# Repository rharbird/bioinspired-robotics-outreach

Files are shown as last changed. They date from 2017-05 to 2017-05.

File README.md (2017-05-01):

# UCL Bioinspired Robotics Summer School 2016

* Pictures here: https://flic.kr/s/aHskDVVoiB
* Note: In 2017 we will use the BBC Micro:bit JavaScript as the programming language for students with https://microbit.pxt.org.

## Snake Robot
* Designed by Dr Juan Gonzalez http://www.thingiverse.com/thing:13442
* C++ libraries for BBC Micro:bit, servo motors and Adafruit PCA9685 board, ( 16-Channel 12-bit PWM/Servo Driver, interface I2C board ) written by Professor Stephen Hailes, UCL.
* Teaching material written by Professor Stephen Hailes, UCL.

## Cockroach Robot
* Designed by Professor Stephen Hailes, UCL.
* C++ libraries for BBC Micro:bit, servo motors and Adafruit PCA9685 board, ( 16-Channel 12-bit PWM/Servo Driver, interface I2C board ) written by Professor Stephen Hailes, UCL.
* Teaching material written by Professor Stephen Hailes, UCL.

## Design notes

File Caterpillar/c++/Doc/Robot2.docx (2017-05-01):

# Microbit projects: caterpillar

## The aim

We’re going to build a crawling robot that’s inspired by some types of caterpillar. See:

https://www.youtube.com/watch?v=fRVGWCSij_M

or

https://www.youtube.com/watch?v=a9Km0edRFG4

In our case, we’ll only have 3 body segments but, as you can see from the video, a wave passes along the caterpillar so we’ll try to mimic that. For this project, we’re going to need some power, provided by a particular type of motor called a servo motor, and we’re going to need to control that using a program written on a MicroBit.

## A sketch

# Skills needed

- Servo motor (PWM)
- Programming

## Let’s begin: Servo Motors

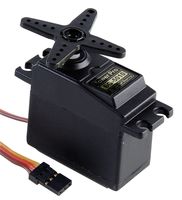
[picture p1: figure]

First we’re going to take a look at the servo motor. There are two types of servo – the first is one where you can choose an angle to which the arms should rotate; the second goes round and round at a speed you set. We’re going to use the first type here and the second type in the next project.

Servos are used all over the place in both daily life and in robotics. A servo might retract the tray of a DVD player or might be used in radio controlled vehicles and aeroplanes to control the rudder of a boat, or the ailerons on a plane. They are a motor we can set to a certain angle – in our case ranging from 0° to 180°.

### PWM

The angle of the motors is set using what is called a pulse width modulation signal (PWM).

0.5ms

0

1.5ms

90

2.5ms

180

20ms

0ms

Time /ms

### Connecting a motor to the microbit

Although the MicroBit can drive upto 3 servo motors, we have decided to use a second board to connect the MicroBit to the servos, for two reasons:

- The MicroBit works on a 3.3V circuit, and the servos work on ~5V. Consequently, we can’t just connect the two together anyway.
- We can connect up to 16 servos to the MicroBit using the interface board – we could make a very long snake

The PWM board communicates with the MicroBit using a special digital communications channel – I²C. We have written some code to hide these details from you.

DO NOT CONNECT THE BATTERY UNTIL YOUR CIRCUIT HAS BEEN CHECKED

The PWM board should be connected to the MicroBit like this:

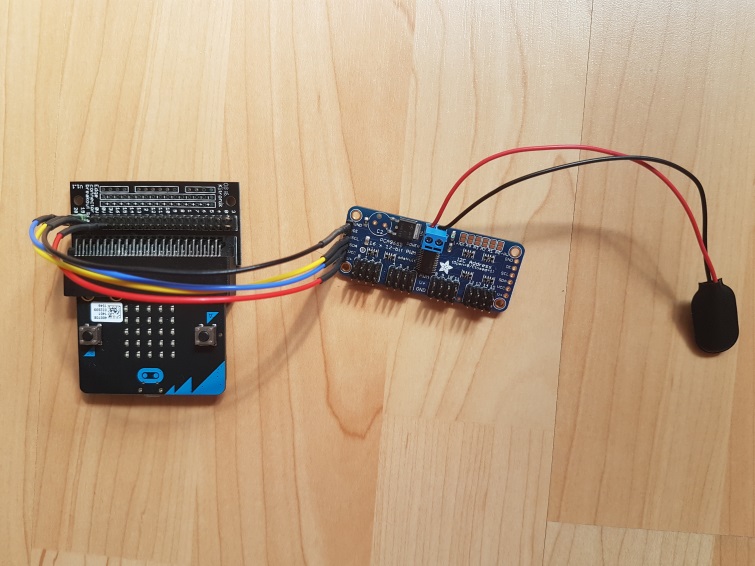
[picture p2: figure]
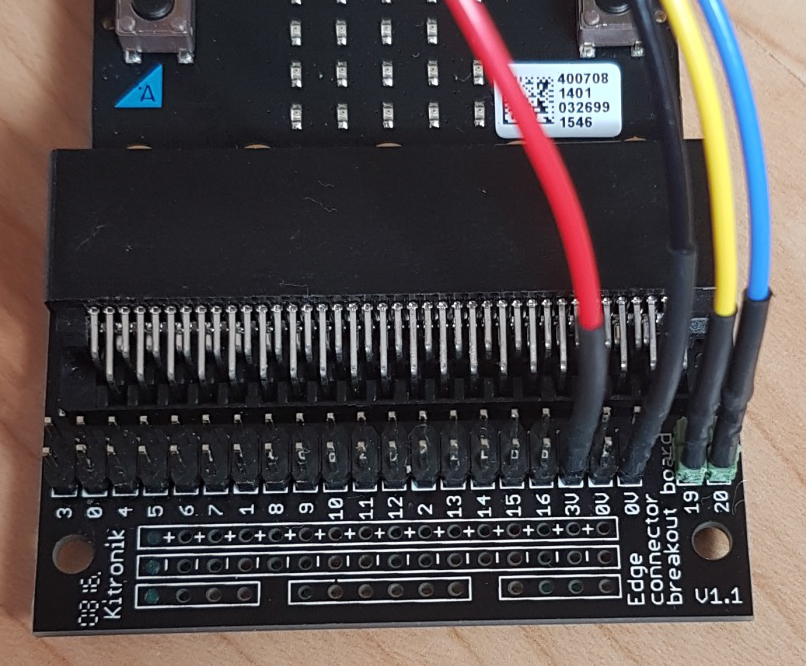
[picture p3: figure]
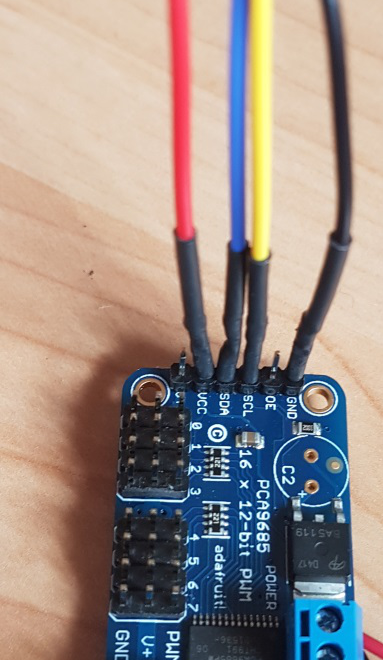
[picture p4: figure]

And the servo(s) should be connected to the pwm board this way round – on the left is a servo connected in position 0. (It’s easier if you start at 0 and work up if you have more servos connected).

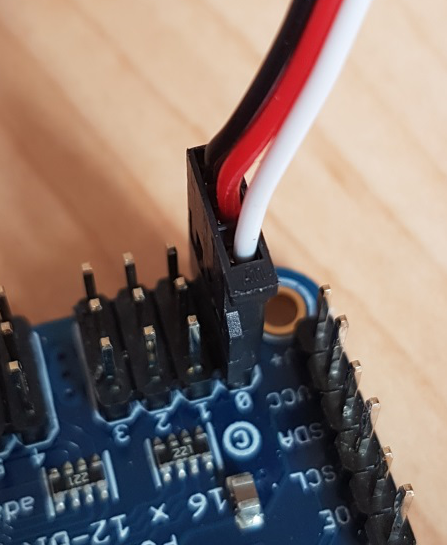
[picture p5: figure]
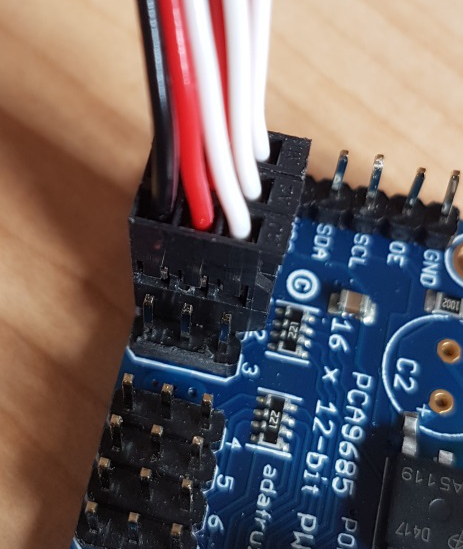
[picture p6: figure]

### Writing code to drive the motors

As I said above, we have written some code to make life a bit easier for you. You can set an angle on a servo like this:

Note the & here

Just idle waiting for an event

When the button is pressed move the servo by 10 degrees

Listen for any button event – call onButton if there is one

1. Create a new project for the MicroBit, called ‘test-servo' and copy the files PCA9685.h PCA9685.cpp into that directory.
2. Type in the following code and save it as test-servo.cpp in the source directory

#include "MicroBit.h"

#include "PCA9685.h"

MicroBit uBit;

PCA9685 pwm(&uBit, angleServo);

int angle = 0;

void onButton(MicroBitEvent)

{

// Set the angle using setAngle

//

angle += 10;

if (angle > 180) angle = 0;

pwm.setAngle(0, angle);

uBit.display.scroll("Angle");

uBit.display.scroll(angle);

}

int main()

{

uBit.init();

uBit.messageBus.listen(MICROBIT_ID_BUTTON_A, MICROBIT_BUTTON_EVT_CLICK, onButton);

// Initialise the angle to zero and turn the pwm on

pwm.setAngle(0, angle);

pwm.start();

while (1)

uBit.sleep(1000);

}

3. Now compile the code and flash it to a MicroBit
4. Connect a single servo to position 0 on the PWM board, and the PWM board to the MicroBit – ask someone to check it for you before connecting the battery.

### extending this

We need to be able to make segments of the snake move forward by lifting and stretching. Conveniently, this turns out to be done just by changing the angles between segments in the caterpillar – but the servo moves way too fast on its own and we need to be able to control it better.

1. Create a new project for the MicroBit, called ‘test-servo2' and copy the same files over.
2. You should write a program to make the servo move slowly and smoothly from one extreme to the other – i.e. from 0° to 180° and back
3. To do this, you could:
  a. break the change angle down into small increments – try a few degrees at a time
  b. make a change and insert a delay before making the next
4. Now compile the code and flash it to the MicroBit

What do you see?

If we look at this on a graph, we see that the changes happen linearly

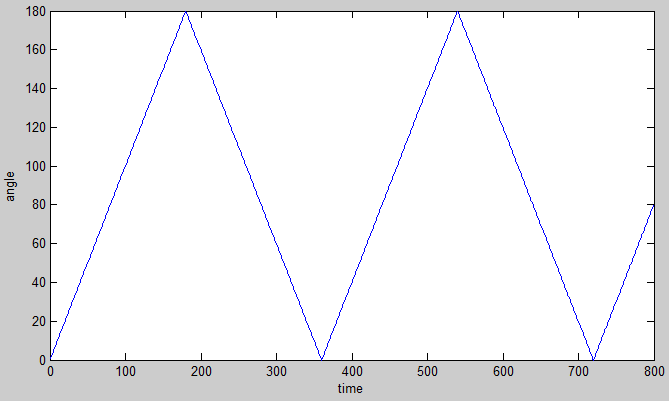
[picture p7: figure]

As it happens, many things in biology happen like sine waves. That’s true for this kind of movement – what we’d like to see is the following

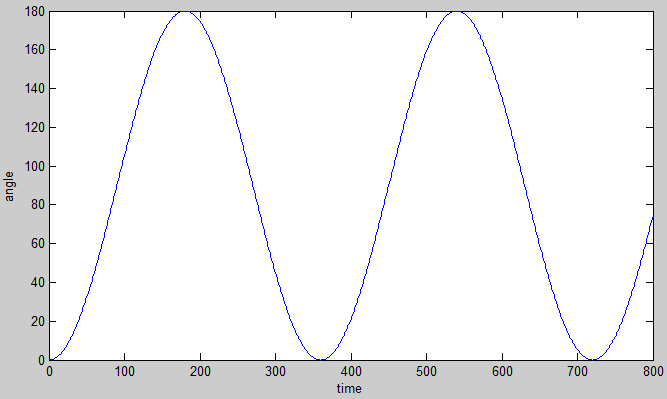
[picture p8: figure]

What this means is that the change in angle is slower the closer you get to 180 and to 0. So, it starts slowly, then gets faster, then slows down, changes direction, and so on.[^1]

1. If we want make a change in angle at time t we need to know what the time is:

long t = uBit.systemTime(); // Gives the time since startup in milliseconds

2. See if you can figure out the angle you should set the servo to – this will be a function of t (remember this is in ms) and will involve a sin function. Useful code:

y = sin(x); // calculates the sine of x, where x is in radians

3. To make life easier, you might like to use the following function:

double degrees2radians(double angle) {

return (angle*PI/180);

}

y = sin(degrees2radians(d)); // Now d is in degrees

4. Answer…. see endnote i

## Oscillator

Congratulations – you made an oscillator.

## Building the snake

Make a snake – it should look like this. There’s one at the front of the room if you need to look

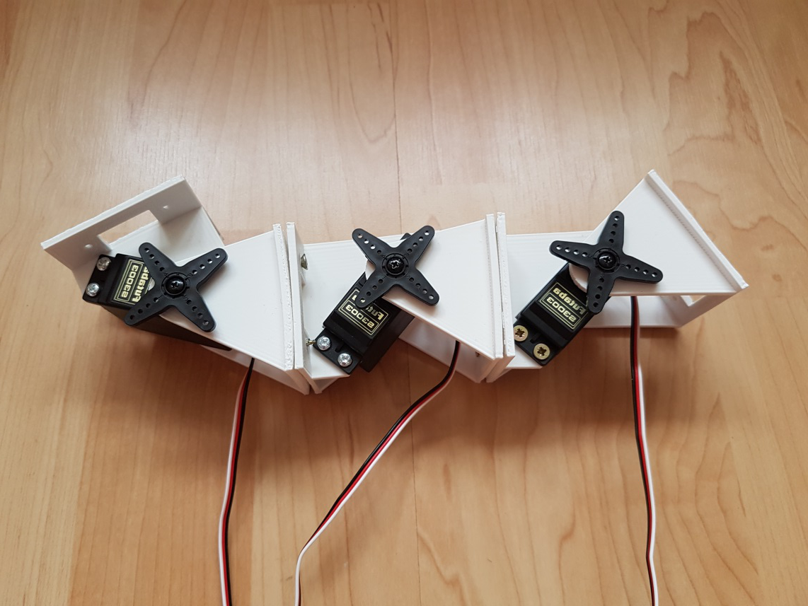
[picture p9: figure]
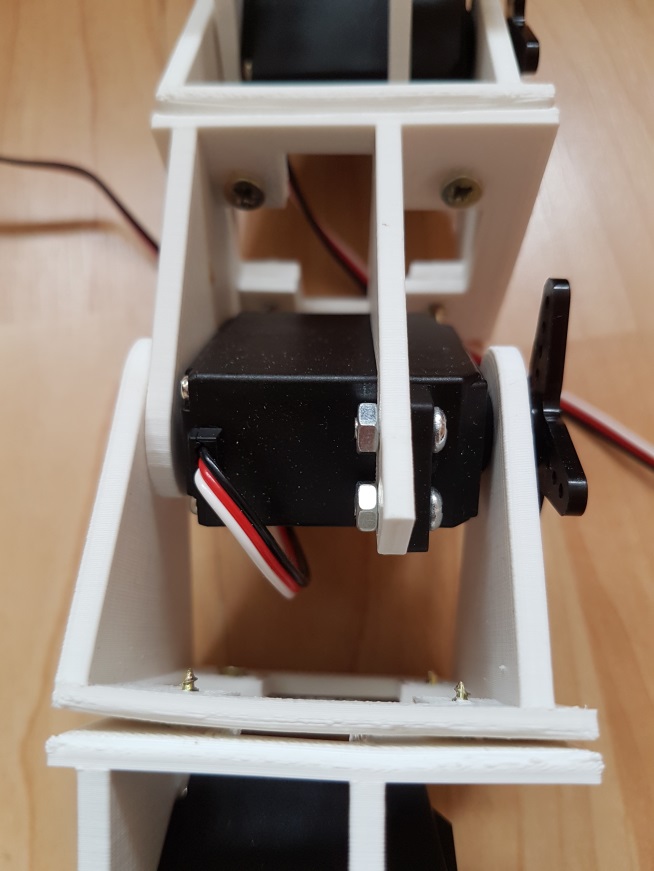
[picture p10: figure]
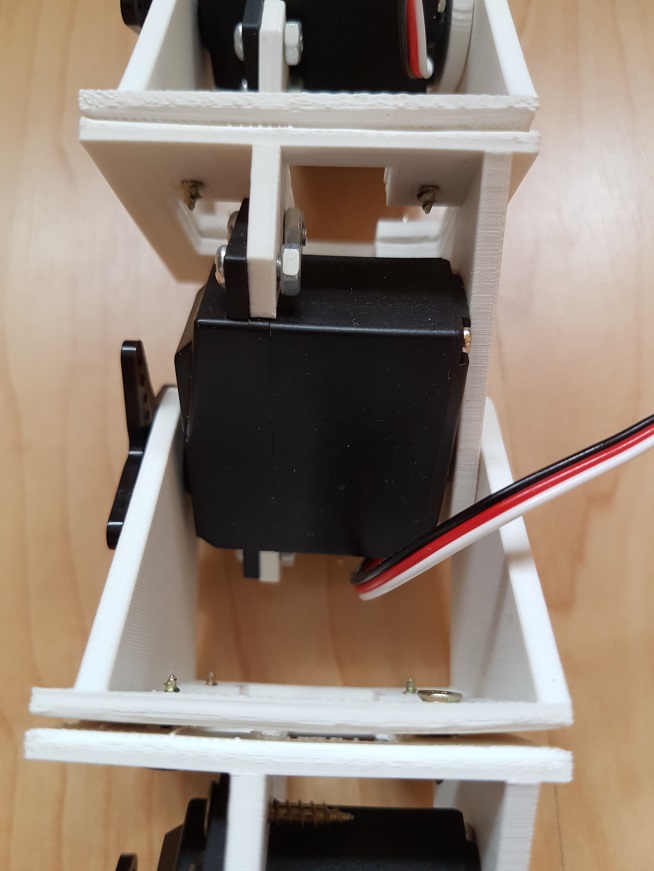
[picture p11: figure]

## Making the caterpillar move

1. Create a new project for the MicroBit, called ‘caterpillar'
2. Make all the servos in the caterpillar move in sync.
3. Does the caterpillar crawl?
4. Take another look at the videos. See if you can figure out what might make the caterpillar work.

## central pattern generators

Central pattern generators (CPGs) are biological neural networks that produce rhythmic patterned outputs without sensory feedback. CPGs have been shown to produce rhythmic outputs resembling normal "rhythmic motor pattern production" even in isolation from motor and sensory feedback from limbs and other muscle targets. To be classified as a rhythmic generator, a CPG requires: 1. "two or more processes that interact such that each process sequentially increases and decreases, and 2. that, as a result of this interaction, the system repeatedly returns to its starting condition. CPGs have been found in practically all vertebrate species investigated, including human. Wikipedia

We’re going to mimic a CPG – the control of movement in the caterpillar will be done with very limited sensory input. The electronics requires us to know the angle of each servo but the same approach would work if all we had was an oscillator (or an oscillator per segment).

## Phase

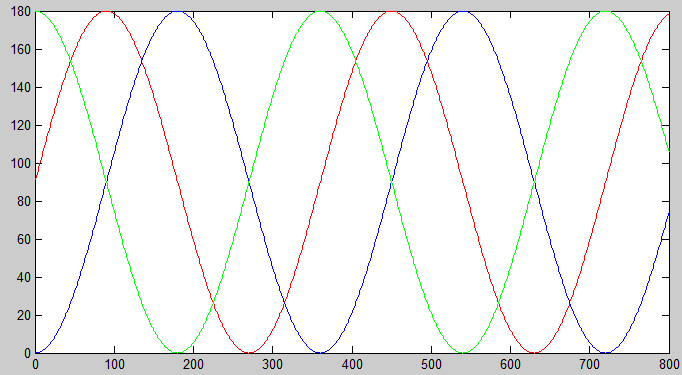
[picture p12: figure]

Here we have three sine waves out of phase with one another. The blue and the green lines are 180° out of phase – completely out of phase: when one is at 180°, the other is at 0° and vice versa. The red line is somewhere in between.

1. If we have one angle calculated from time by:

angle_0 = C + A*sin(degrees2radians(360*t/T));

We can have a second calculated by:

angle_1 = C + A*sin(degrees2radians(360*t/T + P));

where P is an angle between 0° and 360°, depending on what phase difference we want.

2. Can you use this to make the caterpillar move more effectively?

## Competition

1. How fast can you go? Things to think about:
  a. Should each segment move through the same amplitude?
  b. Should we use the same centre position for each segment?
  c. Should the movement of each segment be symmetric?
  d. How fast should the oscillation be?
  e. Can you customise the caterpillar to change the friction between it and the ground?
2. Can you make the robot move on its side?

# Endnotes

[^1] angle = 90 + 90*sin(degrees2radians(360*t/4000)); - t is the system time. - The 4000ms is the amount of time is takes to go from angle zero to zero. Make it bigger to go slower. - sin varies between 0 and 1 so the angle varies between 0° and 180° as things stand. The 90*… is the amplitude – here we want it to go through all 180° of motion. Make this smaller if you want less – if the value was, say 40, then the movement would vary between 60° and 130°. - The 90+… is the centre position of the movement. The servo moves equally either side of that centre. You could choose to centre the movement in a different place. If this was, say, 100 and the amplitude was 40 then the servo would move between 60° and 140°. - You should perhaps create variables for amplitude and time period, say A and T, with another for the centre, C. This makes the formula: angle = C + A*sin(degrees2radians(360*t/T));

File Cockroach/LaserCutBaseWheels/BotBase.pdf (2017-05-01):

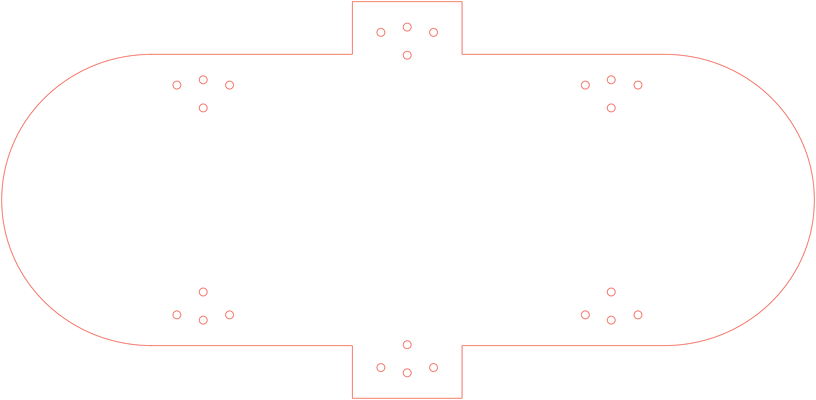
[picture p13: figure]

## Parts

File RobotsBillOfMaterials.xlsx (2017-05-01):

Snake Bill of Materials
 | Quantity | Item | Supplier
 | 1 | BBC Micro:bit | http://uk.farnell.com/bbc-microbit
 | 1 | Micro USB to standard USB connector
 | 1 | Battery cage for 2xAAA batteries | http://uk.farnell.com/kitronik/2271/battery-cage-aaa-battery/dp/2563851
 | 1 | BBC Micro:bit Edge Connector | http://uk.farnell.com/kitronik/5601b/breakout-board-edge-connector/dp/2563845
 | 1 | PCA9685 board 16-Channel 12-bit PWM/Servo Driver - I2C interface | https://www.amazon.co.uk/Adafruit-Channel-Bit-Servo-Driver/dp/B00KLDPYXO
 | 1 | PPV3 9V Battery clip
 | 1 | Battery holder 4xAA with standard snap connector
 | 2 | AAA battery
 | 4 | AA battery
 | 4 | Female to female jumper wires
 | 3 | Futaba S3003 servo motor
 | 3 | 3D printed snake unit | http://www.thingiverse.com/thing:13442
 | 15 | M3, flat head, 10mm steel screw, washer and nut
 | 8 | M3, pan head, 10mm steel screw, washer and nut
Cockroach Bill of Materials
 | Quantity | Item | Supplier
 | 1 | BBC Micro:bit | http://uk.farnell.com/bbc-microbit
 | 1 | Micro USB to standard USB connector
 | 1 | Battery cage for 2xAAA batteries | http://uk.farnell.com/kitronik/2271/battery-cage-aaa-battery/dp/2563851
 | 1 | BBC Micro:bit Edge Connector | http://uk.farnell.com/kitronik/5601b/breakout-board-edge-connector/dp/2563845
 | 1 | PCA9685 board 16-Channel 12-bit PWM/Servo Driver - I2C interface | https://www.amazon.co.uk/Adafruit-Channel-Bit-Servo-Driver/dp/B00KLDPYXO
 | 1 | PPV3 9V Battery clip
 | 1 | Battery holder 4xAA with standard snap connector
 | 2 | AAA battery
 | 4 | AA battery
 | 4 | Female to female jumper wires
 | 6 | Parallax 360 degree continuous servo motor, Product ID: 900-00008
 | 24 | M1, 12mm, steel screw and nut
 | 24 | M4, pan head, 20mm, steel screw, washer and nut
 | 12 | M4, flat head, 20mm, steel screw, washer and nut
 | 6 | 3D printed bracket | See files in folder
 | 6 | 3D printed wheg | See files in folder
 | 6 | 3D printed axel | See files in folder
 | 1 | lasercut body / board | See template in folder

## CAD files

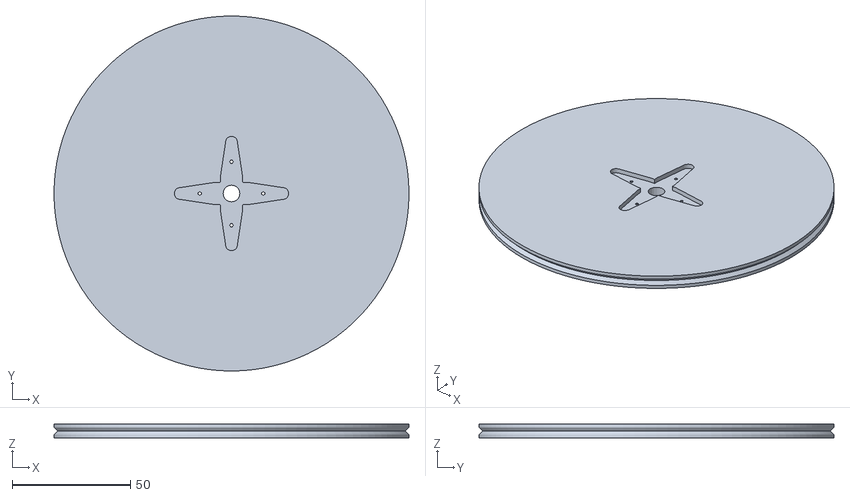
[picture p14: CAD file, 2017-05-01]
Cockroach/3DPrinting/SCAD/STL/servo_wheel.stl
150.0 x 150.0 x 6.00

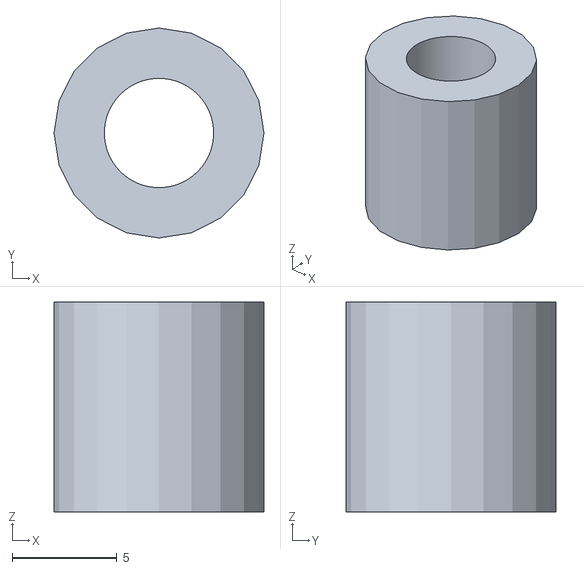
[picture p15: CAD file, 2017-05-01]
Cockroach/3DPrinting/SCAD/STL/axle_cap.stl
10.0 x 10.0 x 10.0

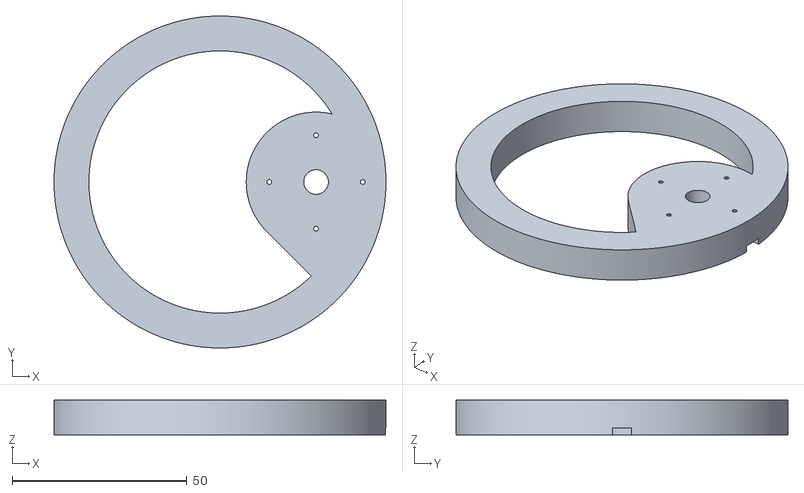
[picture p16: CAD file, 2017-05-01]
Cockroach/3DPrinting/SCAD/STL/right_leg.stl
95.0 x 95.0 x 10.0

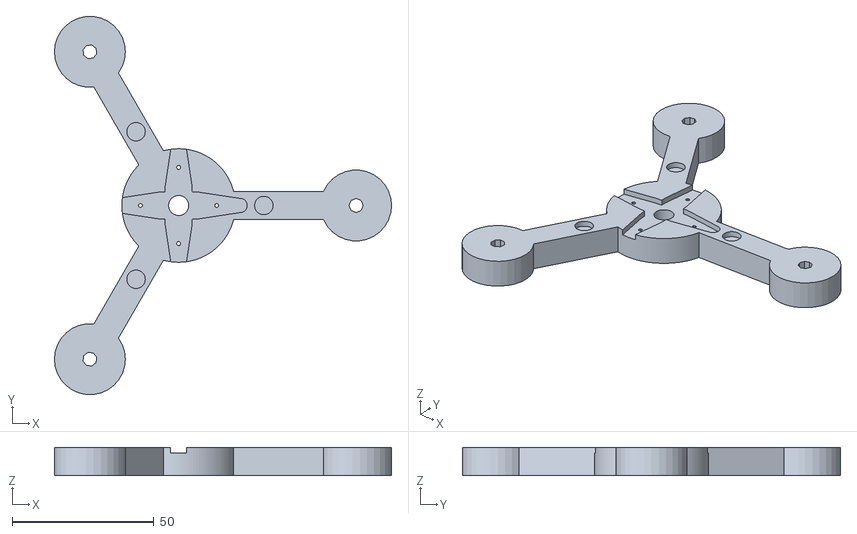
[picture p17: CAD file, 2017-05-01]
Cockroach/3DPrinting/SCAD/STL/trileg_left.stl
118.8 x 133.1 x 10.0

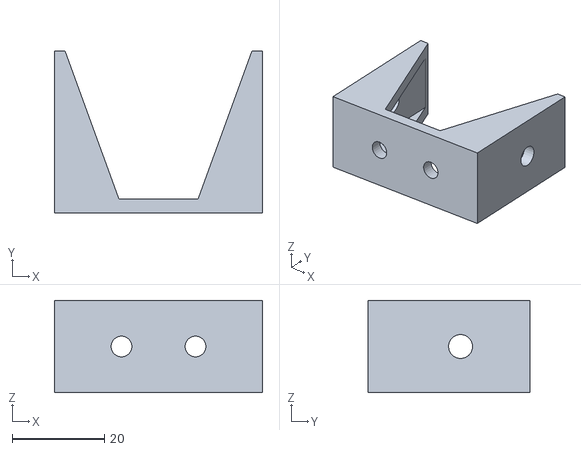
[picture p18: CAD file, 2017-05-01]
Cockroach/3DPrinting/SCAD/STL/axle_bracket.stl
45.0 x 35.0 x 20.0

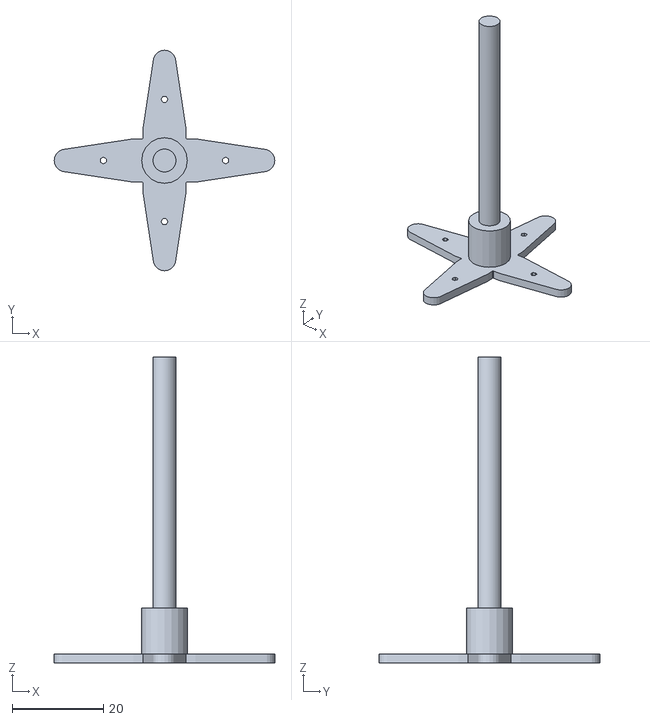
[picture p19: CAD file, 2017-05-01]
Cockroach/3DPrinting/SCAD/STL/axle_and_hub.stl
48.3 x 48.3 x 67.0

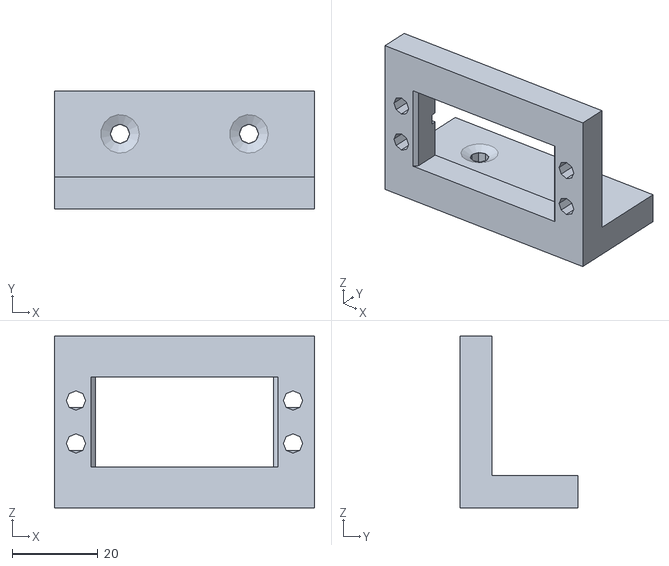
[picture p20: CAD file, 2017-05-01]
Cockroach/3DPrinting/SCAD/STL/900-00008_Servo_Bracket.stl
60.5 x 27.5 x 40.0

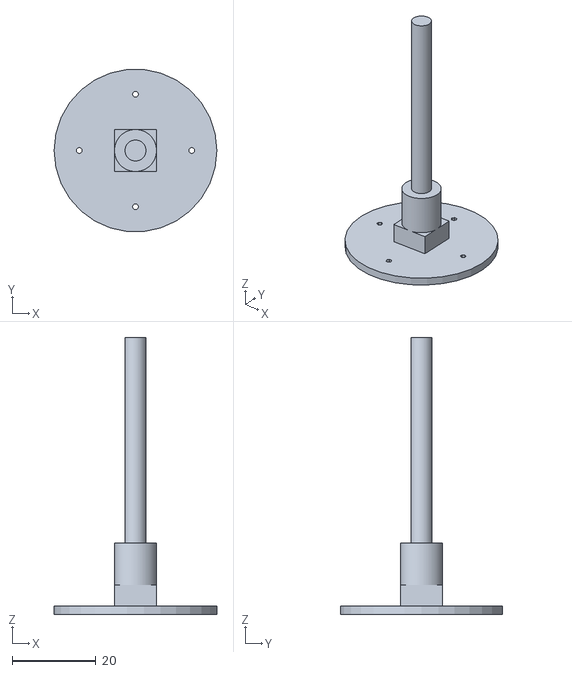
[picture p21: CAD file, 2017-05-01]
Cockroach/3DPrinting/SCAD/STL/AxleAndHub2.stl
38.8 x 38.6 x 66.0

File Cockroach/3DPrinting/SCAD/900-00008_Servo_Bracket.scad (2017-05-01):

// Create the bracket in two parts
//
THICKNESS=7.5;    // Thickness of the walls of the bracket
HOLEDIAMETER=4.5; // Diameter of the holes
SERVOHEIGHT=20;   // How tall the servo motor is when placed side-on to drive legs
SERVOWIDTH=40.5;  // Width of the servo
SERVOSLACK=1;     // How much more room we want to give around the servo in each dimension to allow for each fitting
SIDEWIDTH=10;     // How wide the surround should be
SIDEHOLESEPX=50.5;// x distance between the holes on the side
SIDEHOLESEPZ=10;  // z distance between the holes on the side
BASEHOLESEP=30;   // Distance between the holes on the base of the bracket
BASEDEPTH=20;     // Depth of the projecting part of the base
NOTCHLENGTH=4.5;    // Dimensions of the notch on the rear
NOTCHWIDTH=2.5;
NOTCHDEPTH=1.25;

//Draw a prism based on a 
//right angled triangle
//l - length of prism
//w - width of triangle
//h - height of triangle
module prism(l, w, h) {
       polyhedron(points=[
               [0,0,h],           // 0    front top corner
               [0,0,0],[w,0,0],   // 1, 2 front left & right bottom corners
               [0,l,h],           // 3    back top corner
               [0,l,0],[w,l,0]    // 4, 5 back left & right bottom corners
       ], faces=[ // points for all faces must be ordered clockwise when looking in
               [0,2,1],    // top face
               [3,4,5],    // base face
               [0,1,4,3],  // h face
               [1,2,5,4],  // w face
               [0,3,5,2],  // hypotenuse face
       ]);
}

module bracketSide () {

  difference() {
    // The side
    cube([SIDEWIDTH*2+SERVOWIDTH, THICKNESS, SERVOHEIGHT+SIDEWIDTH*2]);

    union(){      
      // Take out the centre of the side
      // NB might also need to take out the top edge to allow the servo to slot in.
      // In that case, make the z in the cube above SERVOHEIGHT+SIDEWIDTH
      translate([SIDEWIDTH-SERVOSLACK/2, 0, SIDEWIDTH-SERVOSLACK/2])
        cube([SERVOWIDTH+SERVOSLACK, THICKNESS, SERVOHEIGHT+SERVOSLACK]);
      
      // And the holes in the LHS.
      translate([SIDEWIDTH/2,THICKNESS,SIDEWIDTH+(SERVOHEIGHT-SIDEHOLESEPZ)/2])
        rotate([90,0,0])
          cylinder(h=THICKNESS, d=HOLEDIAMETER);
      translate([SIDEWIDTH/2,THICKNESS,SIDEHOLESEPZ+SIDEWIDTH+(SERVOHEIGHT-SIDEHOLESEPZ)/2])
        rotate([90,0,0])
          cylinder(h=THICKNESS, d=HOLEDIAMETER);
      
      // And the holes in the RHS
      translate([1.5*SIDEWIDTH+SERVOWIDTH,THICKNESS,SIDEWIDTH+(SERVOHEIGHT-SIDEHOLESEPZ)/2])
        rotate([90,0,0])
          cylinder(h=THICKNESS, d=HOLEDIAMETER);
      translate([1.5*SIDEWIDTH+SERVOWIDTH,THICKNESS,SIDEHOLESEPZ+SIDEWIDTH+(SERVOHEIGHT-SIDEHOLESEPZ)/2])
        rotate([90,0,0])
          cylinder(h=THICKNESS, d=HOLEDIAMETER);
          
      // And the chamfer on the LHS
      translate([SIDEWIDTH-SERVOSLACK/2, 0, SIDEWIDTH-SERVOSLACK/2])
        rotate([90,0,180])
          prism(SERVOHEIGHT+SERVOSLACK, 1, 1);

      // And the chamfer on the RHS
      translate([SIDEWIDTH+SERVOWIDTH+SERVOSLACK/2, 0, SIDEWIDTH-SERVOSLACK/2])
        rotate([90,0,90])
          prism(SERVOHEIGHT+SERVOSLACK, 1, 1);
          
      // And the LHS rear notch
      translate([SIDEWIDTH-NOTCHLENGTH,THICKNESS-NOTCHDEPTH,SIDEWIDTH+SERVOHEIGHT/2-NOTCHWIDTH/2])
        cube([NOTCHLENGTH, NOTCHDEPTH, NOTCHWIDTH]);
      
      // And the RHS rear notch
      // And the LHS rear notch
      translate([SIDEWIDTH+SERVOWIDTH+SERVOSLACK/2,THICKNESS-NOTCHDEPTH,SIDEWIDTH+SERVOHEIGHT/2-NOTCHWIDTH/2])
        cube([NOTCHLENGTH, NOTCHDEPTH, NOTCHWIDTH]);
      
    }
  }
}

module bracketBase() {
  difference() {
    // The base
    cube([SERVOWIDTH+2*SIDEWIDTH, THICKNESS+BASEDEPTH, THICKNESS]);
    
    union() {
      // Holes
      translate([(SERVOWIDTH+2*SIDEWIDTH-BASEHOLESEP)/2, THICKNESS+BASEDEPTH/2, 0]) {
        cylinder(h=THICKNESS, d=HOLEDIAMETER);
      }
      translate([(SERVOWIDTH+2*SIDEWIDTH+BASEHOLESEP)/2, THICKNESS+BASEDEPTH/2, 0]) {
        cylinder(h=THICKNESS, d=HOLEDIAMETER);
      }
      // And countersinks
      translate([(SERVOWIDTH+2*SIDEWIDTH-BASEHOLESEP)/2, THICKNESS+BASEDEPTH/2, THICKNESS-HOLEDIAMETER/4]) {
        cylinder(h=HOLEDIAMETER/4, d1=HOLEDIAMETER, d2=HOLEDIAMETER*2);
      }
      translate([(SERVOWIDTH+2*SIDEWIDTH+BASEHOLESEP)/2, THICKNESS+BASEDEPTH/2, THICKNESS-HOLEDIAMETER/4]) {
        cylinder(h=HOLEDIAMETER/4, d1=HOLEDIAMETER, d2=HOLEDIAMETER*2);
      }
      
    }
  }
}

union() {
  bracketSide();
  bracketBase();
}

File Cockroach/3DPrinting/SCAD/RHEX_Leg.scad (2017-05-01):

// Thickness of the leg - used everywhere
leg_thickness=10;

//-- Parameters common to all horns
horn_drill_diam   = 1.5;
horn_plate_height = 2;              //-- plate height
horn_height       = leg_thickness;  //-- Total height: shaft + plate

//-- Parallax 900-0008 4-arm horn parameters
a4h_end_diam       = 5;
a4h_center_diam    = 9.5;
a4h_arm_length     = 19.4;
a4h_drill_distance = 13.4;


// Flag - leg on the left (0) or right (1). Side is given if you
// were standing at the back of the robot looking towards its front
side = 0;

// Leg arc
leg_radius=42.5;
leg_width=10;

// Hub
hub_diameter=40;
hub_screw_diameter=7.05;

// Embedded magnets; spacing is how much gap to add around the magnet
// Dimensions website. However, not clear if these are radii or diameter
magnet_spacing = 0.5;
magnet_diameter = 6 + magnet_spacing;
magnet_thickness = 1.5 + magnet_spacing;

hub_x = leg_radius-hub_diameter/2+leg_width/2;
hub_radius = 0.5 * hub_diameter;
hub_thickness=leg_thickness;

magnet_x_1 = hub_x - hub_radius/2;
magnet_x_2 = hub_x + hub_radius/2;
magnet_z = (side == 0) ? (leg_thickness - magnet_thickness)/2 : -(leg_thickness - magnet_thickness)/2;

// Chamfer between hub and leg
theta=-45;

// Point on the hub where the chamfer starts
xc = hub_x - hub_radius*cos(theta);
yc = hub_radius*sin(theta);

inner_leg_radius = leg_radius + 0.5 * leg_width;

// Solve quadratric for where the chamfer finishes
a = 1;
b = 2*(xc*cos(theta)+yc*sin(theta));
c = xc * xc + yc * yc - inner_leg_radius * inner_leg_radius;
r = 0.5 * (-b + sqrt(b*b-4*a*c));

module raw_leg()
{ 
  // The leg
  rotate([180,0,0]) rotate_extrude(angle = 180, convexity=2,$fn=360)
  translate([leg_radius, 0, 0])
  square(size=[leg_width, leg_thickness],center=true);
  
  // The end cap on the leg
  translate([-leg_radius, 0 ,0])
  cylinder(h=hub_thickness,d=leg_width, $fn=120, center=true);
  
  // The hub
  translate([hub_x, 0 ,0])
  cylinder(h=hub_thickness,d=hub_diameter, $fn=120, center=true);
  
  // The chamfer connecting the hub to the leg
  translate([xc, yc, -leg_thickness*0.5])
  linear_extrude(height=leg_thickness)
  polygon(points=[[0, 0], [r*cos(theta), r*sin(theta)], [r*cos(theta),0]]);
}

module screw_hole()
{
  // The screw hole
  translate([hub_x, 0 ,0])
  cylinder(h=hub_thickness,d=hub_screw_diameter, $fn=120, center=true);  
}

module magnets()
{
  // One magnet
  translate([magnet_x_1, hub_radius/2, magnet_z])
  cylinder(h=magnet_thickness,d=magnet_diameter, $fn=120, center=true);


  // The other magnet
  translate([magnet_x_2, -hub_radius/2, magnet_z])
  cylinder(h=magnet_thickness,d=magnet_diameter, $fn=120, center=true);
}

//--------------------------------------------------------------
//-- Generic module for the horn's drills
//-- Parameters:
//--  d = drill's radial distance (from the horn's center)
//--  n = number of drills
//--  h = wheel height
//--------------------------------------------------------------
module horn_drills(d,n,h)
{
  translate([hub_x,0,horn_height-horn_plate_height])  
    union() {
      for ( i = [0 : n-1] ) {
          rotate([0,0,i*360/n])
          translate([0,d,0])
          cylinder(r=horn_drill_diam/2, h=h+10,center=true, $fn=6);  
        }
    }
}

//-----------------------------------------
//-- Parallax 900-0008 horn4 arm
//-- This module is just one arm
//-----------------------------------------
module horn4_arm(h=5)
{
  translate([0,a4h_arm_length-a4h_end_diam/2,0])
  //-- The arm consist of the perimeter of a cylinder and a cube
  hull() {
    cylinder(r=a4h_end_diam/2, h=h, center=true, $fn=20);
    translate([0,1-a4h_arm_length+a4h_end_diam/2,0])
      cube([a4h_center_diam,2,h],center=true);
  }
}

//-------------------------------------------
//-- Parallax 900-0008 4-arm horn
//-------------------------------------------
module horn4(h=5)
{
  translate([hub_x,0,horn_height-horn_plate_height])
    union() {
      //-- Center part (is a square)
      cube([a4h_center_diam+0.2,a4h_center_diam+0.2,h],center=true);

      //-- Place the 4 arms in every side of the cube
      for ( i = [0 : 3] ) {
        rotate( [0,0,i*90])
        translate([0, a4h_center_diam/2, 0])
        horn4_arm(h);
      }
    }
}



difference() {
  // Make the basic leg
  raw_leg();
  screw_hole();
  magnets();

  //-- substract the 4-arm servo horn
  if (side == 1) {
    mirror([0,0,1])
      horn4(h=leg_thickness);
  } else {
      horn4(h=leg_thickness);    
  }
  
  horn_drills(d=a4h_drill_distance, n=4, h=leg_thickness*2);
}

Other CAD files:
Cockroach/3DPrinting/SCAD/STL/left_leg.stl
Cockroach/3DPrinting/SCAD/STL/trileg_right.stl
Cockroach/3DPrinting/SCAD/Servo-wheel.scad
Cockroach/3DPrinting/SCAD/TriLeg.scad
Cockroach/3DPrinting/SCAD/AxleAndHub.scad
Cockroach/3DPrinting/SCAD/AxleAndHub2.scad
Cockroach/3DPrinting/SCAD/AxleBracket.scad
Cockroach/3DPrinting/SCAD/AxleCap.scad

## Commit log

2017-04-30 Materials for UCL's Bioinspired Robotics Summer School
    [900-00008_Servo_Bracket.scad, 900-00008_Servo_Bracket.stl, AxleAndHub.scad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]
2017-05-01 Add README and LICENSE
    [900-00008_Servo_Bracket.scad, 900-00008_Servo_Bracket.stl, AxleAndHub.scad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]
